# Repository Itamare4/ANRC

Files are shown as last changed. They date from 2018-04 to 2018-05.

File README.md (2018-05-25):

ANRC (Autonomous Nitro RC)
------------------------
<p align="center">
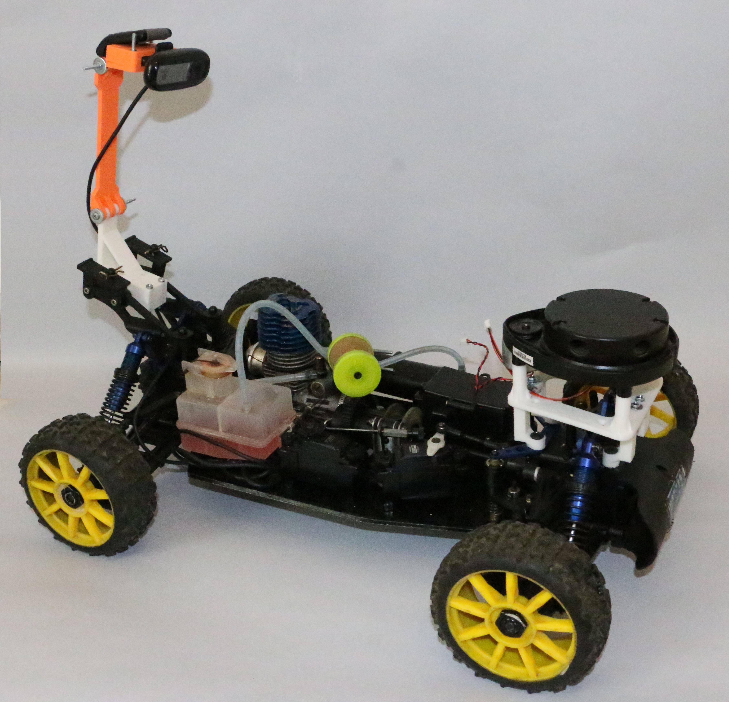
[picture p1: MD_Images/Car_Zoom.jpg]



</p>

### Contacts ###
Itamar Eliakim <br>

### Goal ###
Got an old RC car platform that wasnt in use for around ~10 years. Project goal is to implement algorithms for localization, lane tracking, steering etc. and creating a tiny nitro self-driving car.

### Hardware ###
* Nitro RC Car Platform
* Neato XV-11 Lidar
* Logitech C170
* Orange Pi Lite (AllWinner H3), might change later to BeagleBone
* STM32F103C8
* FlySky i6
* Lipo 7.4v 2200mah
* LM2596 - 5V 3A Buck Regulator
* AMS1117 - 5V to 3.3V (Powering XV11 DC Motor)
* For DIY Electric starter - High torque DC motor (took mine from an old neato)

### Tools/Connectors Needed ###
* 3D printer
* crimp tool
* XT60 Connectors
* PCB Breadboard
* Soldering Station

### Software ###
* Ubuntu 16.04 LTS
* ROS Kinetic

### Experiments ###

### Videos ###

### About ###
Itamar Eliakim<br>
Tel Aviv, Israel<br>
Email - Itamare@gmail.com

Detailed Changelog
------------------------
<p align="center">

</p>

### #3 ###
Wrote a ROS package in python for processing the image from the Logitech C170 (Code available on GitHub). In most example codes available online it's easier to detect the lane by filtering out the lane colors(white, yellow), here i did it in a narrow street so i didn't have many colors to filter out.
<p align="center">

</p>

Based on the great tutorial of Galen Ballew:
https://medium.com/@galen.ballew/opencv-lanedetection-419361364fc0

I had to do many modification so it will work without filtering the yellow and white colors, I've used the following steps:

1. Convert to HSV
2. Filter out background colors.
3. Calculating Sobel magnitude.
4. Flood Fill.
5. Split to left and right image.
5. Manually find contours.
6. Draw a line for the left and right edge.

I got the following result:
<p align="center">

</p>

Running Yolo object detection, with VOC weights on the image(offline), we got the following result - 
<p align="center">

</p>

### #2 ###
I had to record some bagfiles to start working on the lane tracking, auto steering of the car. To make things easier i thought of connecting the Flysky RC to a simple python code and by toggle the switch on the remote start and pause the rosbag record process.
Connecting the Flysky RC to OrangePi sounds like an easy task, had some issues with sampling the PWM signal from the remote at frequency high enough to determine the switch state(This can be done easly on Raspberry Pi using pigpio), if you have some ADC to I2C you can do it easly, something like ADS1115, or just playing with RC circuit.<br>
I didn't have enough time to spend on it, so a simple Arduino Nano was perfect for this task. Routing the SWD on Flysky to CH6 on the reciever and connecting it to PIN 6 on the Arduino.<br>
The python code for reading values for Arduino and starting the record sometimes doesnt end cleanly(will be fixed later), need to run this on the bags - 
```
rosbag reindex *.bag.active
rosbag fix *.bag.active repaired.bag
```

### #1 ###
### Mechanical ###
Getting the RC Car ready to go after ~10 years, engine compression seems to be good, carburetor is completely cleaned. Found out the car didn’t start because of a small pin between the crankshaft and the backplate, when pulling the cord, it rotated only the shaft at the backplate. Instead of ordering a new spring/pull mechanism (didn’t have the patience) just put some Teflon tape between the crankshaft and the small pin, it worked perfectly.    
<p align="center">
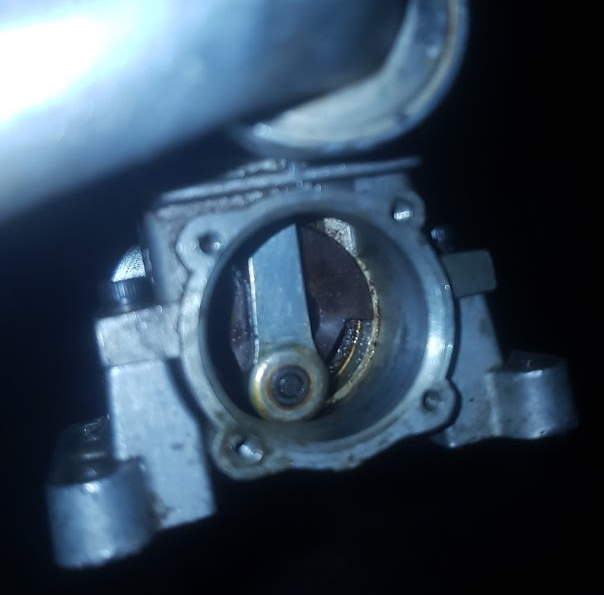
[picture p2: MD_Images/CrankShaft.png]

</p>
Next, designing the parts, I’ve separated this to three major units:<br>
Rear Unit: Webcam, Lights(Later).<br>
Center Unit: Power Regulators (5V and 3.3V), Power Distribution Board, RC Receiver.<br>
Front Unit: Battery, XV11 Lidar, Orange Pi.<br><br>

### Hardware ###
**Rear Unit:**  
1x Logitech C170  
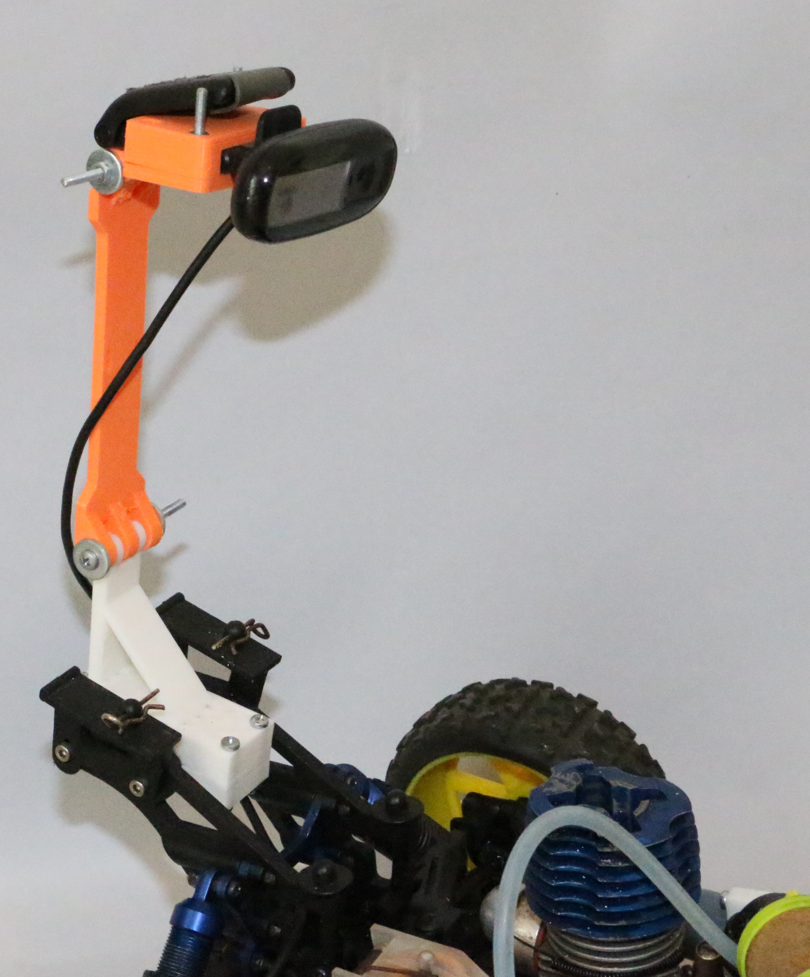
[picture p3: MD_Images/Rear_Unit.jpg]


**Center Unit:**  
Main power supply – LIPO 7.4 2200mah <br>
several components at this design works at 5V/3.3, will use two different regulators:<br>  
1xLM2596 – 5V 3A Buck converter  
1xAMS1117 – 3.3V 800mA Buck converter  
<p align="center">

</p>

<p align="center">

</p>

| PIN  | Details  |
|---|---|
| 1 | 5V from power regulator, pin 10  |
| 2 | GND, pin 11 |
| 3 | 5V - Orange PI|
| 4 | GND - Orange PI |
| 5 | 5V RC Receiver |
| 6 | GND RC Receiver |
| 7 | 3.3V output |
| 8 | 7.4V 2200mah LIPO battery |
| 9 |  GND |

**Front Unit:**    
1x Orange Pi Lite(Allwinner H3)  
1x XV11 Neato Lidar  
1x STM32F103C8  
<p align="center">

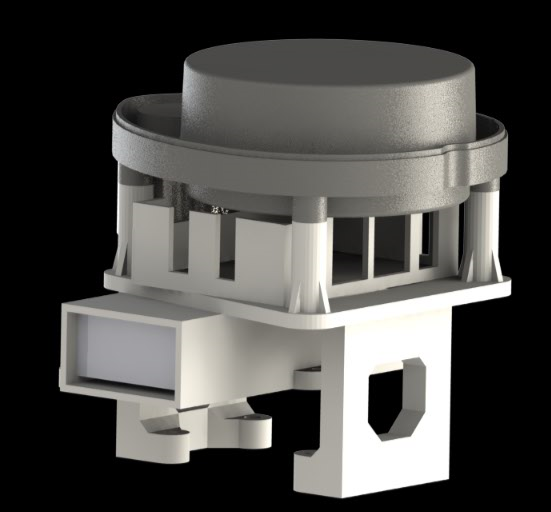
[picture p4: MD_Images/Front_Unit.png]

</p>

### Software ###
1.	Install Armbian for Orange Pi from here:
[https://www.armbian.com/orange-pi-lite/]( https://www.armbian.com/orange-pi-lite/)
2.	Install ROS kinetic
```
echo "deb http://packages.ros.org/ros/ubuntu $(lsb_release -sc) main" >ros-latest.list
sudo cp ros-latest.list /etc/apt/sources.list.d/
sudo apt-key adv --keyserver hkp://ha.pool.sks-keyservers.net:80 --recv-key 421C365BD9FF1F717815A3895523BAEEB01FA116
sudo apt-get update
sudo apt-get install ros-kinetic-ros-base
sudo rosdep init
rosdep update
```

Congratulations, you have ROS kinetic running on your Orange PI. Add some of the basic ROS packages, such as Hector SLAM, and the drivers to XV11, based on this tutorial:
 [http://meetjanez.splet.arnes.si/2015/08/22/neato-xv-11-to-ros-slam/]( http://meetjanez.splet.arnes.si/2015/08/22/neato-xv-11-to-ros-slam/)

Got the XV11 lidar work on the Nitro RC, example of the Laserscan:
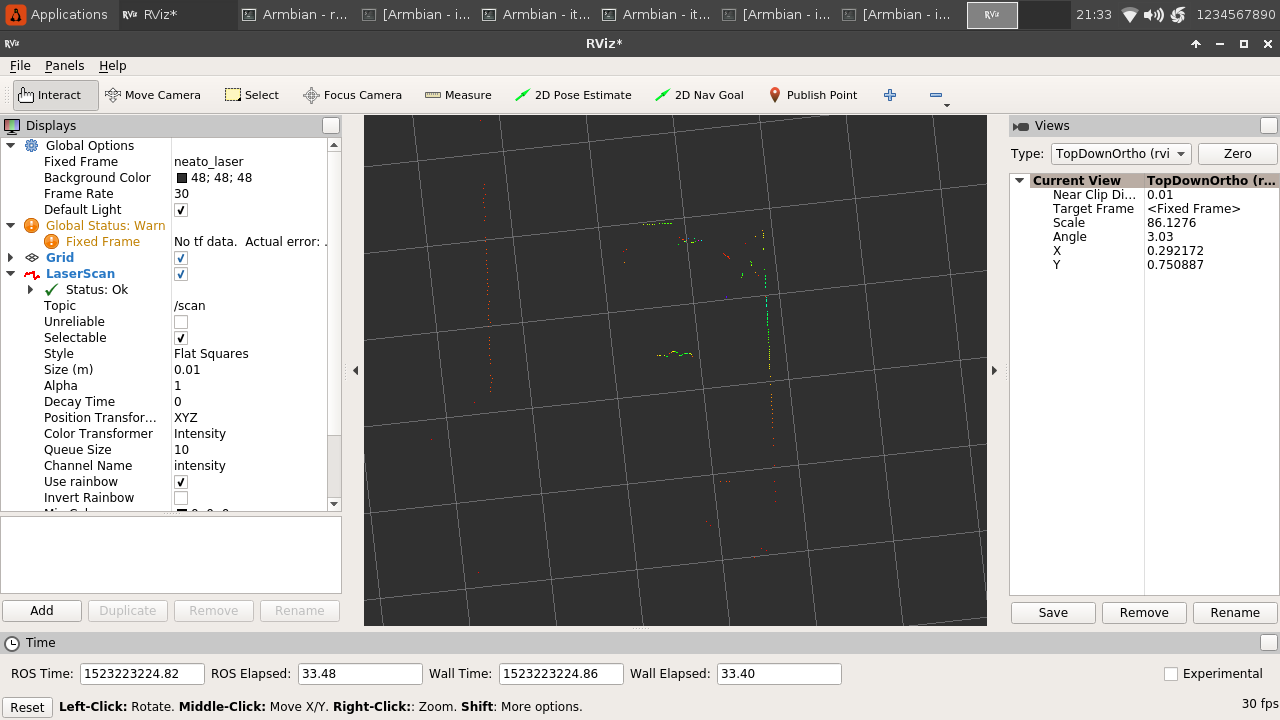
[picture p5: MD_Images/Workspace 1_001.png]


Next weeks:
1.	Check how slow can the car move, XV11 lidar works at really really low speed compare to the speed of the car, will need to see if we can use this lidar or just replace it with a better RGB camera.
2.	Stress test the poor Orange Pi to see if we can use this or will need to change to a better one.
3.	DIY Electric starter.
4.	Record some videos form the webcam so we can start working on the lane tracking, and autonomous steering.

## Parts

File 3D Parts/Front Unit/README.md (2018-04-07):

ANRC (Autonomous Nitro RC)
------------------------

Credits:
Top Part - XV11 Lidar Mount by deadsy - https://www.thingiverse.com/thing:1707495

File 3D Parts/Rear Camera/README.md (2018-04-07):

ANRC (Autonomous Nitro RC)
------------------------

Credits:
Top Part - Logitech C170 webcam holder for ultimaker 2 by zankuro - https://www.thingiverse.com/thing:1464811

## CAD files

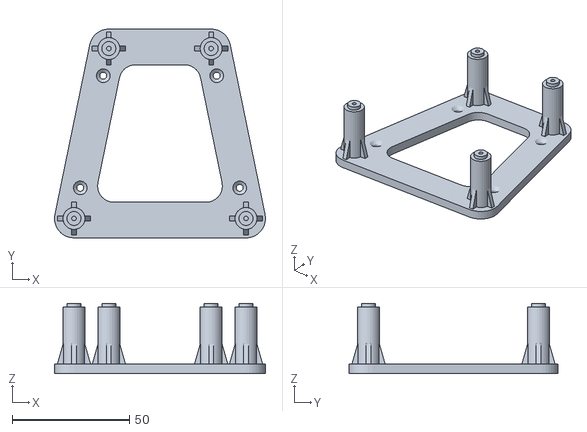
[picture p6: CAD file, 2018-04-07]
3D Parts/Front Unit/xv11_lidar.stl
90.2 x 89.3 x 30.0

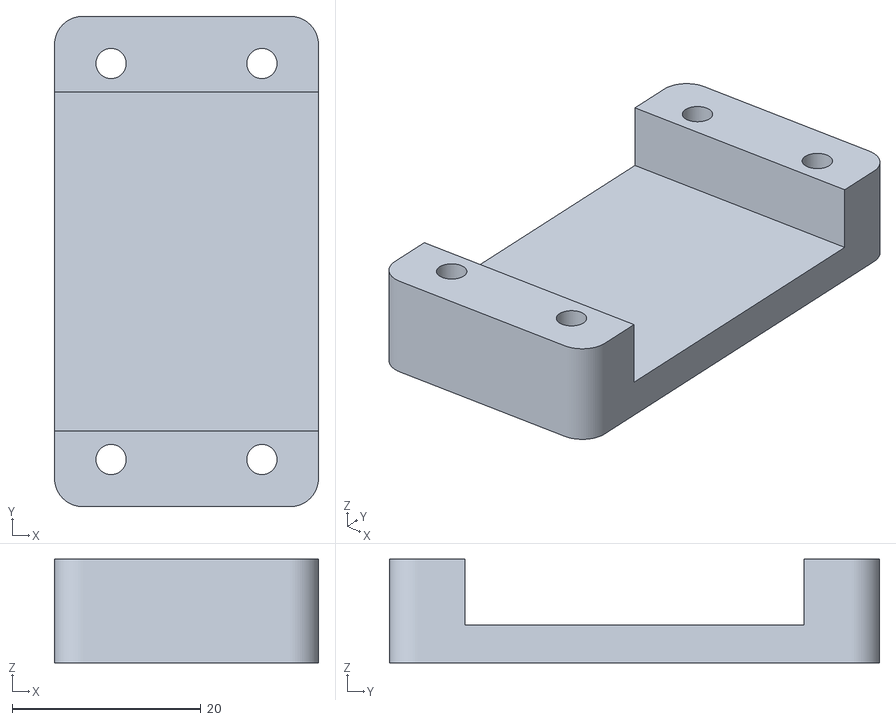
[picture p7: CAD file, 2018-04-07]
3D Parts/Rear Camera/HolderPlate-Buttom.STL
28.0 x 52.0 x 11.0

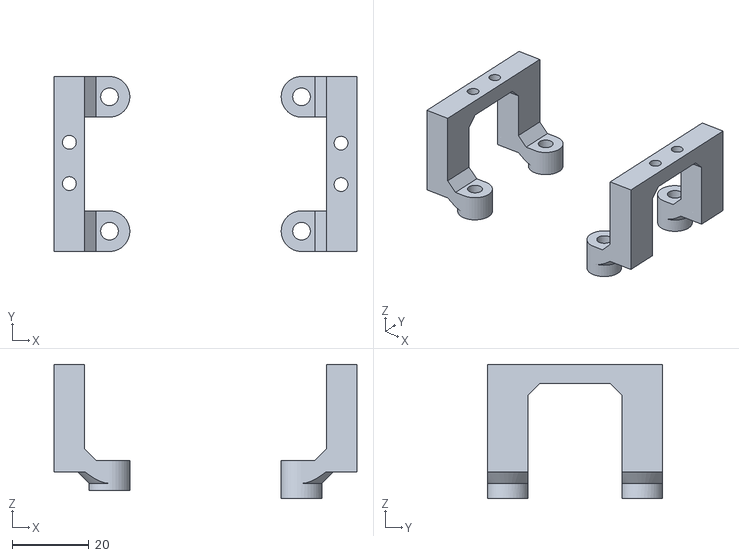
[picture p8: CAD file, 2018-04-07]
3D Parts/Front Unit/xv11_base.STL
78.9 x 45.6 x 35.0

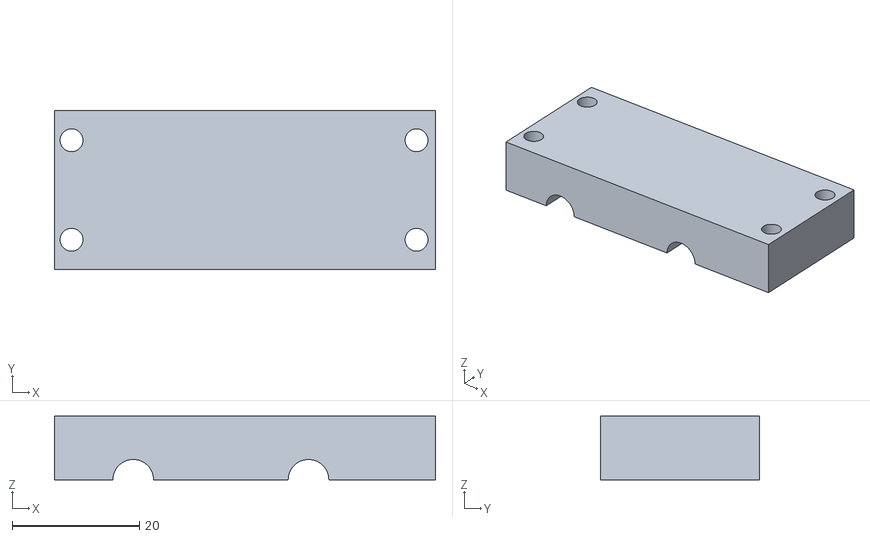
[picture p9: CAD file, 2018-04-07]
3D Parts/Rear Camera/CarHolder-Bottom_C170.STL.STL
60.0 x 25.0 x 10.0

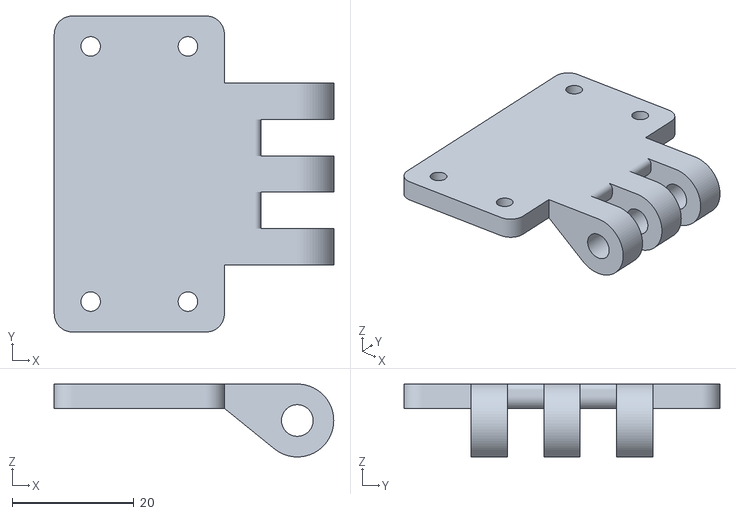
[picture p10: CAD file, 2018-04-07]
3D Parts/Rear Camera/HolderPlate-Top.STL
46.0 x 52.0 x 12.0

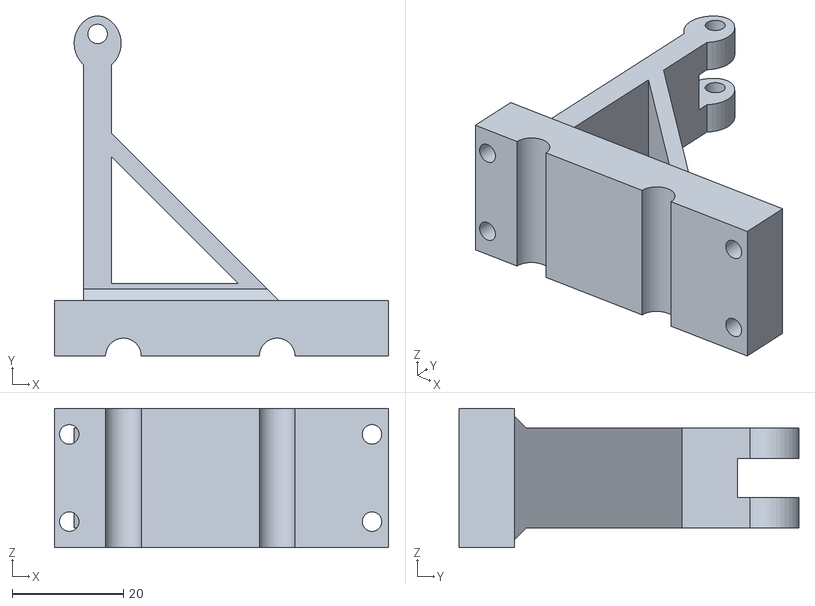
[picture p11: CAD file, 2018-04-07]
3D Parts/Rear Camera/CarHolder-Top_C170.STL
60.0 x 61.0 x 25.0

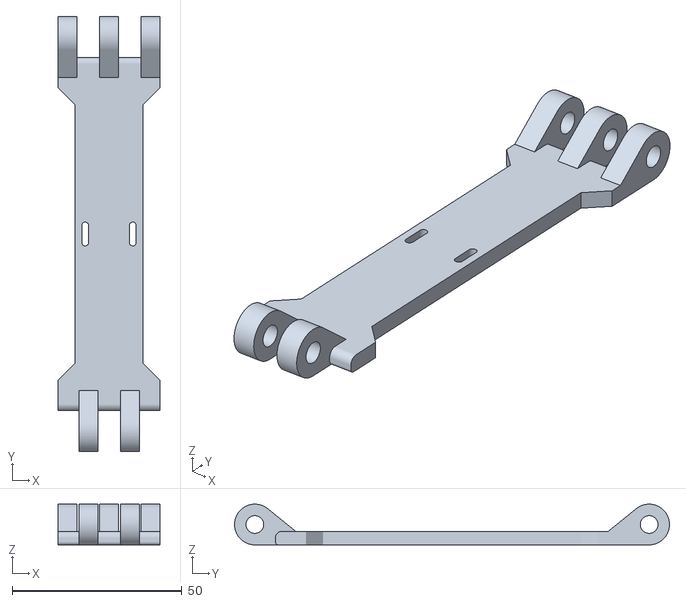
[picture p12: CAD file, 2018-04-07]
3D Parts/Rear Camera/P01_Arm1.STL
30.0 x 128.0 x 12.0

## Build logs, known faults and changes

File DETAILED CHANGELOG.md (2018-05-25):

ANRC (Autonomous Nitro RC)    
Detailed Changelog
------------------------
<p align="center">

</p>

### #3 ###
Wrote a ROS package in python for processing the image from the Logitech C170 (Code available on GitHub). In most example codes available online it's easier to detect the lane by filtering out the lane colors(white, yellow), here i did it in a narrow street so i didn't have many colors to filter out.
<p align="center">

</p>

Based on the great tutorial of Galen Ballew:
https://medium.com/@galen.ballew/opencv-lanedetection-419361364fc0

I had to do many modification so it will work without filtering the yellow and white colors, I've used the following steps:

1. Convert to HSV
2. Filter out background colors.
3. Calculating Sobel magnitude.
4. Flood Fill.
5. Split to left and right image.
5. Manually find contours.
6. Draw a line for the left and right edge.

I got the following result:
<p align="center">

</p>

Running Yolo object detection, with VOC weights on the image(offline), we got the following result - 
<p align="center">

</p>

### #2 ###
I had to record some bagfiles to start working on the lane tracking, auto steering of the car. To make things easier i thought of connecting the Flysky RC to a simple python code and by toggle the switch on the remote start and pause the rosbag record process.
Connecting the Flysky RC to OrangePi sounds like an easy task, had some issues with sampling the PWM signal from the remote at frequency high enough to determine the switch state(This can be done easly on Raspberry Pi using pigpio), if you have some ADC to I2C you can do it easly, something like ADS1115, or just playing with RC circuit.<br>
I didn't have enough time to spend on it, so a simple Arduino Nano was perfect for this task. Routing the SWD on Flysky to CH6 on the reciever and connecting it to PIN 6 on the Arduino.<br>
The python code for reading values for Arduino and starting the record sometimes doesnt end cleanly(will be fixed later), need to run this on the bags - 
```
rosbag reindex *.bag.active
rosbag fix *.bag.active repaired.bag
```

### #1 ###
### Mechanical ###
Getting the RC Car ready to go after ~10 years, engine compression seems to be good, carburetor is completely cleaned. Found out the car didn’t start because of a small pin between the crankshaft and the backplate, when pulling the cord, it rotated only the shaft at the backplate. Instead of ordering a new spring/pull mechanism (didn’t have the patience) just put some Teflon tape between the crankshaft and the small pin, it worked perfectly.    
<p align="center">

</p>
Next, designing the parts, I’ve separated this to three major units:<br>
Rear Unit: Webcam, Lights(Later).<br>
Center Unit: Power Regulators (5V and 3.3V), Power Distribution Board, RC Receiver.<br>
Front Unit: Battery, XV11 Lidar, Orange Pi.<br><br>

### Hardware ###
**Rear Unit:**  
1x Logitech C170  


**Center Unit:**  
Main power supply – LIPO 7.4 2200mah, several components at this design works at 5V/3.3, will use two different regulators:  
1xLM2596 – 5V 3A Buck converter  
1xAMS1117 – 3.3V 800mA Buck converter  
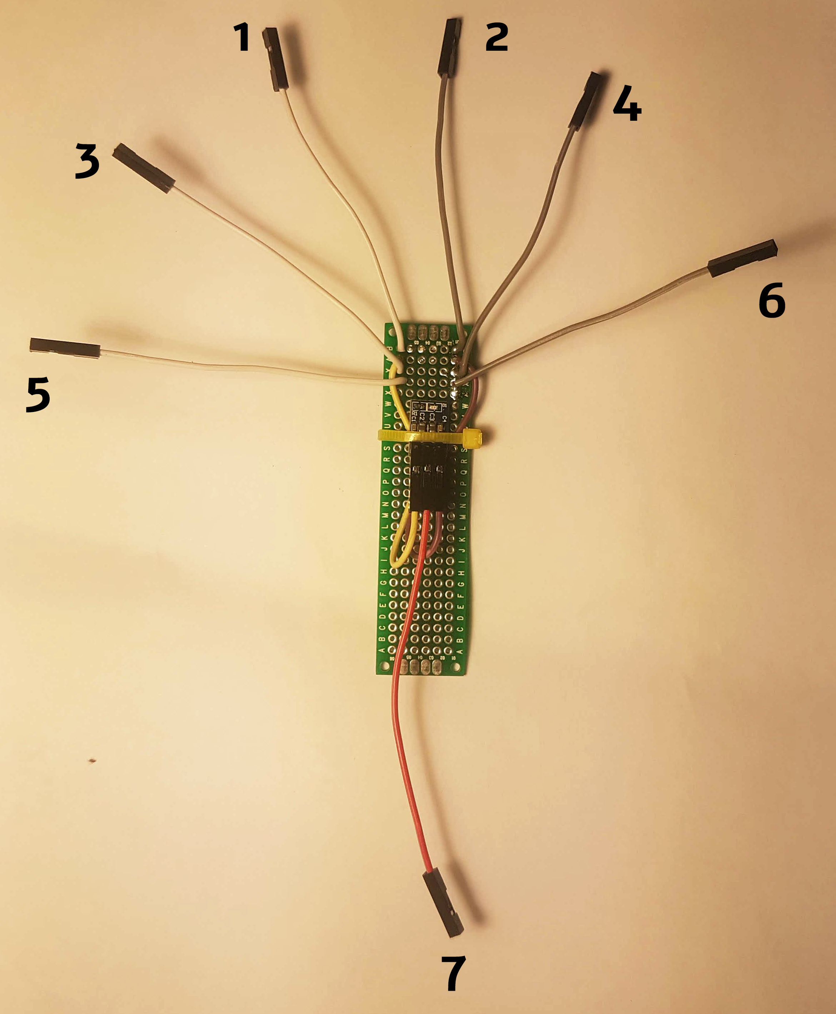
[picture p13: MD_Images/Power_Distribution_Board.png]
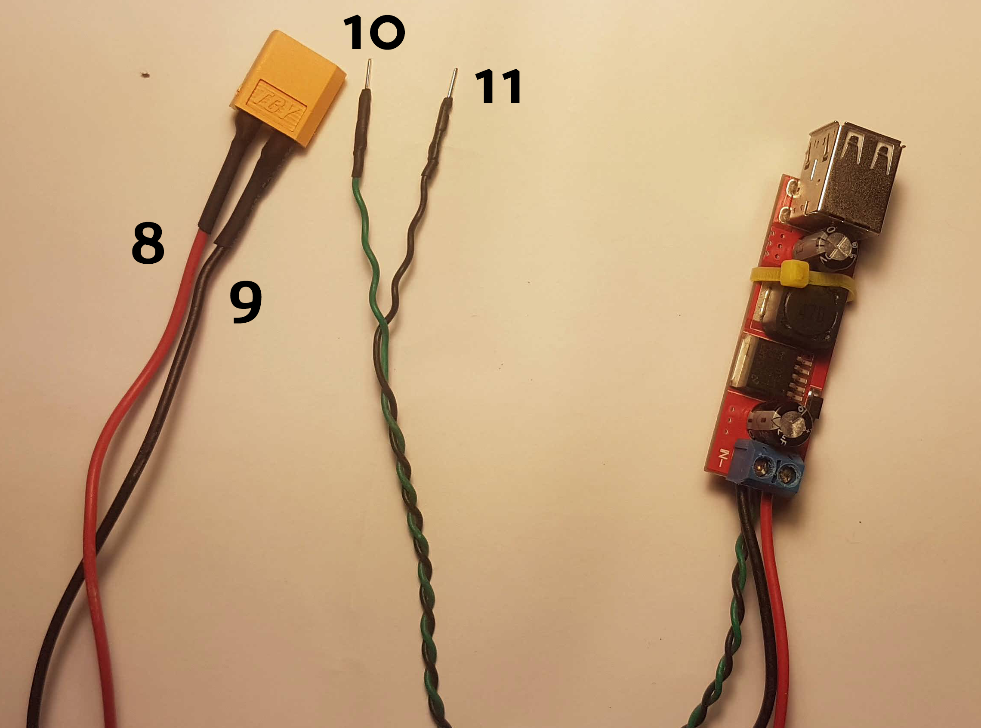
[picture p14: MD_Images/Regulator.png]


| PIN  | Details  |
|---|---|
| 1 | 5V from power regulator, pin 10  |
| 2 | GND, pin 11 |
| 3 | 5V - Orange PI|
| 4 | GND - Orange PI |
| 5 | 5V RC Receiver |
| 6 | GND RC Receiver |
| 7 | 3.3V output |
| 8 | 7.4V 2200mah LIPO battery |
| 9 |  GND |

**Front Unit:**    
1x Orange Pi Lite(Allwinner H3)  
1x XV11 Neato Lidar  
1x STM32F103C8  
<p align="center">


</p>

### Software ###
1.	Install Armbian for Orange Pi from here:
[https://www.armbian.com/orange-pi-lite/]( https://www.armbian.com/orange-pi-lite/)
2.	Install ROS kinetic
```
echo "deb http://packages.ros.org/ros/ubuntu $(lsb_release -sc) main" >ros-latest.list
sudo cp ros-latest.list /etc/apt/sources.list.d/
sudo apt-key adv --keyserver hkp://ha.pool.sks-keyservers.net:80 --recv-key 421C365BD9FF1F717815A3895523BAEEB01FA116
sudo apt-get update
sudo apt-get install ros-kinetic-ros-base
sudo rosdep init
rosdep update
```

Congratulations, you have ROS kinetic running on your Orange PI. Add some of the basic ROS packages, such as Hector SLAM, and the drivers to XV11, based on this tutorial:
 [http://meetjanez.splet.arnes.si/2015/08/22/neato-xv-11-to-ros-slam/]( http://meetjanez.splet.arnes.si/2015/08/22/neato-xv-11-to-ros-slam/)

Got the XV11 lidar work on the Nitro RC, example of the Laserscan:


Next weeks:
1.	Check how slow can the car move, XV11 lidar works at really really low speed compare to the speed of the car, will need to see if we can use this lidar or just replace it with a better RGB camera.
2.	Stress test the poor Orange Pi to see if we can use this or will need to change to a better one.
3.	DIY Electric starter.
4.	Record some videos form the webcam so we can start working on the lane tracking, and autonomous steering.
